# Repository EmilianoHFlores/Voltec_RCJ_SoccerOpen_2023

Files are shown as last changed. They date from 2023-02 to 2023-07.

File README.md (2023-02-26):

# Voltec_RCJ_SoccerOpen_2023
 Source programs. libraries, electronic schematicsm designs and CAD files from the 2023 Voltec Robocup team, participating in TMR 2023 Soccer Open category.

## Arduino Programs
 All arduino libraries and programs are created for running on an ATMEGA-2560 chip. For pin assignments, refer to the pcb schematics and design.

## PCBs
 PCB design files were created on Autodesk Eagle 9.6.2. Library requirements and references are included on folder.

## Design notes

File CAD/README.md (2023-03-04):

## CAD Development
 Full robot design is available at Onshape:  https://cad.onshape.com/documents/feb5a52ba7614c4b1a7fc88d/w/56c9259f389f981d8cc47606/e/bcdc579321adfbcaa5aa0d92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

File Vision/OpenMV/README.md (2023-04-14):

## Development
 All programs in OpenMV vision have been tested on an OPENMV H7 R2 camera and an OPENMV H7 R1. Only standard camera libraries have been used.

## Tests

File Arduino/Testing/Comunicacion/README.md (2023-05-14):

# Comunicación entre arduino y openmv
Este es el sistema de comunicación utilizado entre el controlador y la cámara para transmitir datos de manera organizada
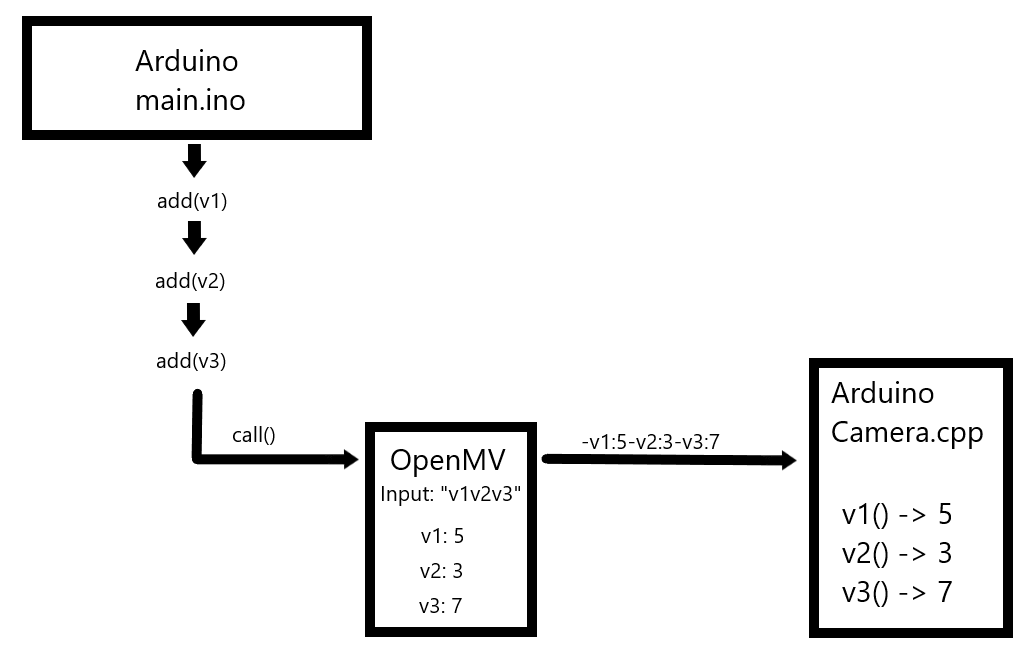
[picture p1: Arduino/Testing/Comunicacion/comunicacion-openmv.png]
Sistema de comunicación entre Arduino y OpenMV

* Ejemplo utilizando Javascript

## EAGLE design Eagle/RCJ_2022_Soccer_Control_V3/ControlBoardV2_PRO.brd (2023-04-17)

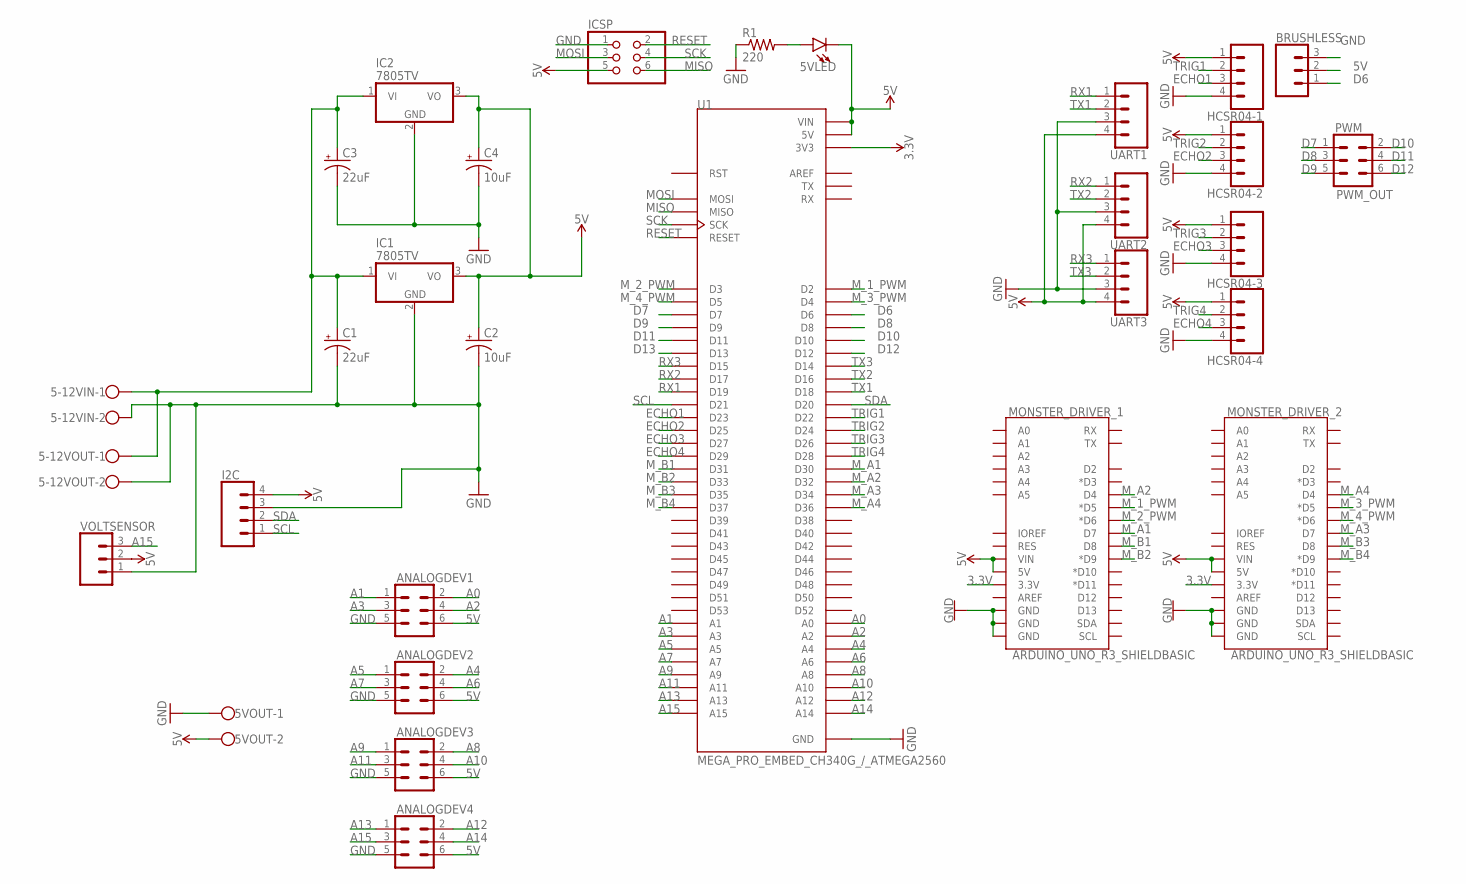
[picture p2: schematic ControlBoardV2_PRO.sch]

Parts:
5-12VIN, 5-12VOUT, 5VOUT: W237-102
5VLED: LED5MM; LED_5MM
ANALOGDEV1, ANALOGDEV2, ANALOGDEV3, ANALOGDEV4: CONN_03X2NO_SILK; 2X3-NS
BRUSHLESS: CONN_03; 1X03
C1, C3: 22uF; E2,5-5
C2, C4: 10uF; E2,5-5
HCSR04-1, HCSR04-2, HCSR04-3, HCSR04-4: CONN_04; 1X04
I2C: CONN_04; 1X04
IC1, IC2: 7805TV; TO220V
ICSP: PINHD-2X3; 2X03
MONSTER_DRIVER_1, MONSTER_DRIVER_2: ARDUINO_UNO_R3_SHIELDBASIC; UNO_R3_SHIELD
PWM: PWM_OUT; 2X3
R1: 220; 0204/7
U1: MEGA_PRO_EMBED_CH340G_/_ATMEGA2560; MODULE_MEGA_PRO_EMBED_CH340G_/_ATMEGA2560
UART1, UART2, UART3: CONN_04; 1X04
VOLTSENSOR: CONN_03; 1X03

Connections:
3.3V: MONSTER_DRIVER_1.3.3V, MONSTER_DRIVER_2.3.3V, U1.3V3_1 (3V3), U1.3V3_2 (3V3)
5V: 5VLED.K (C), 5VOUT.2, ANALOGDEV1.6, ANALOGDEV2.6, ANALOGDEV3.6, ANALOGDEV4.6, BRUSHLESS.2, C2.+, C4.+, HCSR04-1.1, HCSR04-2.1, HCSR04-3.1, HCSR04-4.1, I2C.4, IC1.3 (VO), IC2.3 (VO), ICSP.5, MONSTER_DRIVER_1.5V, MONSTER_DRIVER_1.VIN, MONSTER_DRIVER_2.5V, MONSTER_DRIVER_2.VIN, U1.5V_1 (5V), U1.5V_2 (5V), U1.5V_3 (5V), U1.VIN_1 (VIN), U1.VIN_2 (VIN), UART1.4, UART2.4, UART3.4, VOLTSENSOR.2
A0: ANALOGDEV1.2, U1.A0
A1: ANALOGDEV1.1, U1.A1
A2: ANALOGDEV1.4, U1.A2
A3: ANALOGDEV1.3, U1.A3
A4: ANALOGDEV2.2, U1.A4
A5: ANALOGDEV2.1, U1.A5
A6: ANALOGDEV2.4, U1.A6
A7: ANALOGDEV2.3, U1.A7
A8: ANALOGDEV3.2, U1.A8
A9: ANALOGDEV3.1, U1.A9
A10: ANALOGDEV3.4, U1.A10
A11: ANALOGDEV3.3, U1.A11
A12: ANALOGDEV4.2, U1.A12
A13: ANALOGDEV4.1, U1.A13
A14: ANALOGDEV4.4, U1.A14
A15: ANALOGDEV4.3, U1.A15, VOLTSENSOR.3
D6: BRUSHLESS.1, U1.D6
D7: PWM.1, U1.D7
D8: PWM.3, U1.D8
D9: PWM.5, U1.D9
D10: PWM.2, U1.D10
D11: PWM.4, U1.D11
D12: PWM.6, U1.D12
D13: U1.D13
ECHO1: HCSR04-1.3, U1.D23
ECHO2: HCSR04-2.3, U1.D25
ECHO3: HCSR04-3.3, U1.D27
ECHO4: HCSR04-4.3, U1.D29
GND: 5-12VIN.2, 5-12VOUT.2, 5VOUT.1, ANALOGDEV1.5, ANALOGDEV2.5, ANALOGDEV3.5, ANALOGDEV4.5, BRUSHLESS.3, C1.-, C2.-, C3.-, C4.-, HCSR04-1.4, HCSR04-2.4, HCSR04-3.4, HCSR04-4.4, I2C.3, IC1.2 (GND), IC2.2 (GND), ICSP.1, MONSTER_DRIVER_1.GND@0 (GND), MONSTER_DRIVER_1.GND@1 (GND), MONSTER_DRIVER_1.GND@2 (GND), MONSTER_DRIVER_2.GND@0 (GND), MONSTER_DRIVER_2.GND@1 (GND), MONSTER_DRIVER_2.GND@2 (GND), R1.1, U1.GND_1 (GND), U1.GND_2 (GND), U1.GND_3 (GND), UART1.3, UART2.3, UART3.3, VOLTSENSOR.1
MISO: ICSP.6, U1.MISO
MOSI: ICSP.3, U1.MOSI
M_1_PWM: MONSTER_DRIVER_1.D5 (*D5), U1.D2
M_2_PWM: MONSTER_DRIVER_1.D6 (*D6), U1.D3
M_3_PWM: MONSTER_DRIVER_2.D5 (*D5), U1.D4
M_4_PWM: MONSTER_DRIVER_2.D6 (*D6), U1.D5
M_A1: MONSTER_DRIVER_1.D7, U1.D30
M_A2: MONSTER_DRIVER_1.D4, U1.D32
M_A3: MONSTER_DRIVER_2.D7, U1.D34
M_A4: MONSTER_DRIVER_2.D4, U1.D36
M_B1: MONSTER_DRIVER_1.D8, U1.D31
M_B2: MONSTER_DRIVER_1.D9 (*D9), U1.D33
M_B3: MONSTER_DRIVER_2.D8, U1.D35
M_B4: MONSTER_DRIVER_2.D9 (*D9), U1.D37
unnamed: 5VLED.A, R1.2
unnamed: 5-12VIN.1, 5-12VOUT.1, C1.+, C3.+, IC1.1 (VI), IC2.1 (VI)
RESET: ICSP.2, U1.RESET
RX1: U1.D19, UART1.1
RX2: U1.D17, UART2.1
RX3: U1.D15, UART3.1
SCK: ICSP.4, U1.SCK
SCL: I2C.1, U1.D21
SDA: I2C.2, U1.D20
TRIG1: HCSR04-1.2, U1.D22
TRIG2: HCSR04-2.2, U1.D24
TRIG3: HCSR04-3.2, U1.D26
TRIG4: HCSR04-4.2, U1.D28
TX1: U1.D18, UART1.2
TX2: U1.D16, UART2.2
TX3: U1.D14, UART3.2

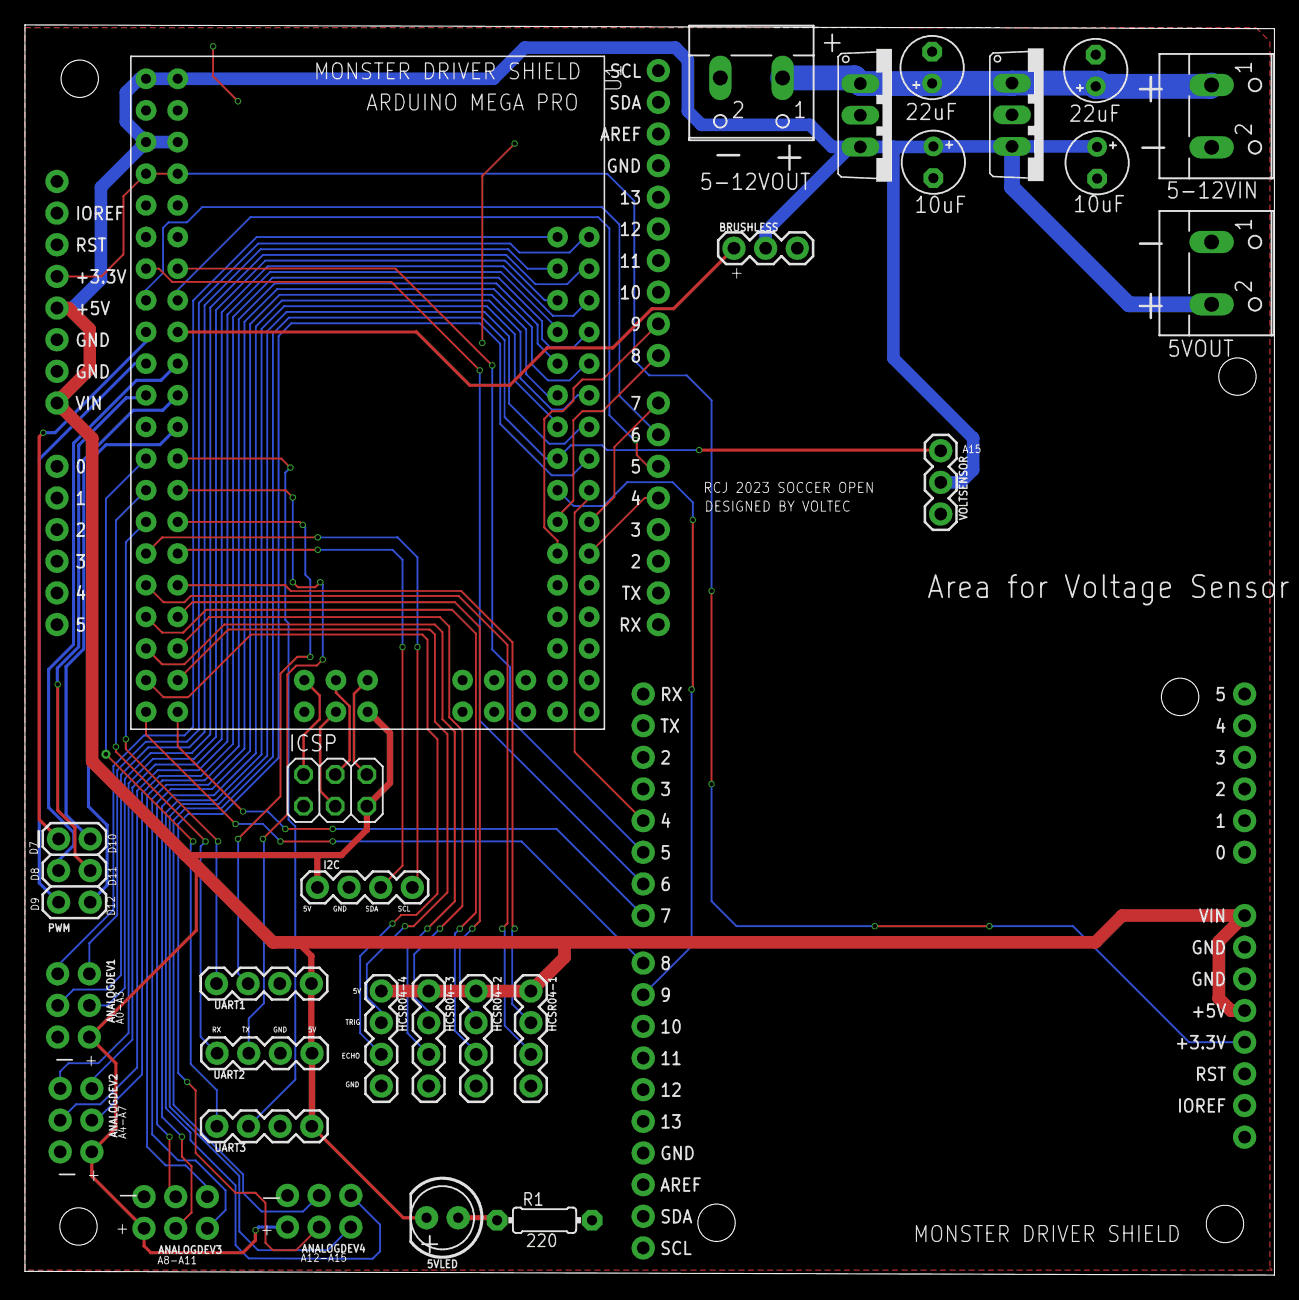
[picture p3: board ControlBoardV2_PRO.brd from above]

Board: 2 copper layers, 100.3 x 100.3 mm, 30 parts (0 on the bottom side), 60 nets.

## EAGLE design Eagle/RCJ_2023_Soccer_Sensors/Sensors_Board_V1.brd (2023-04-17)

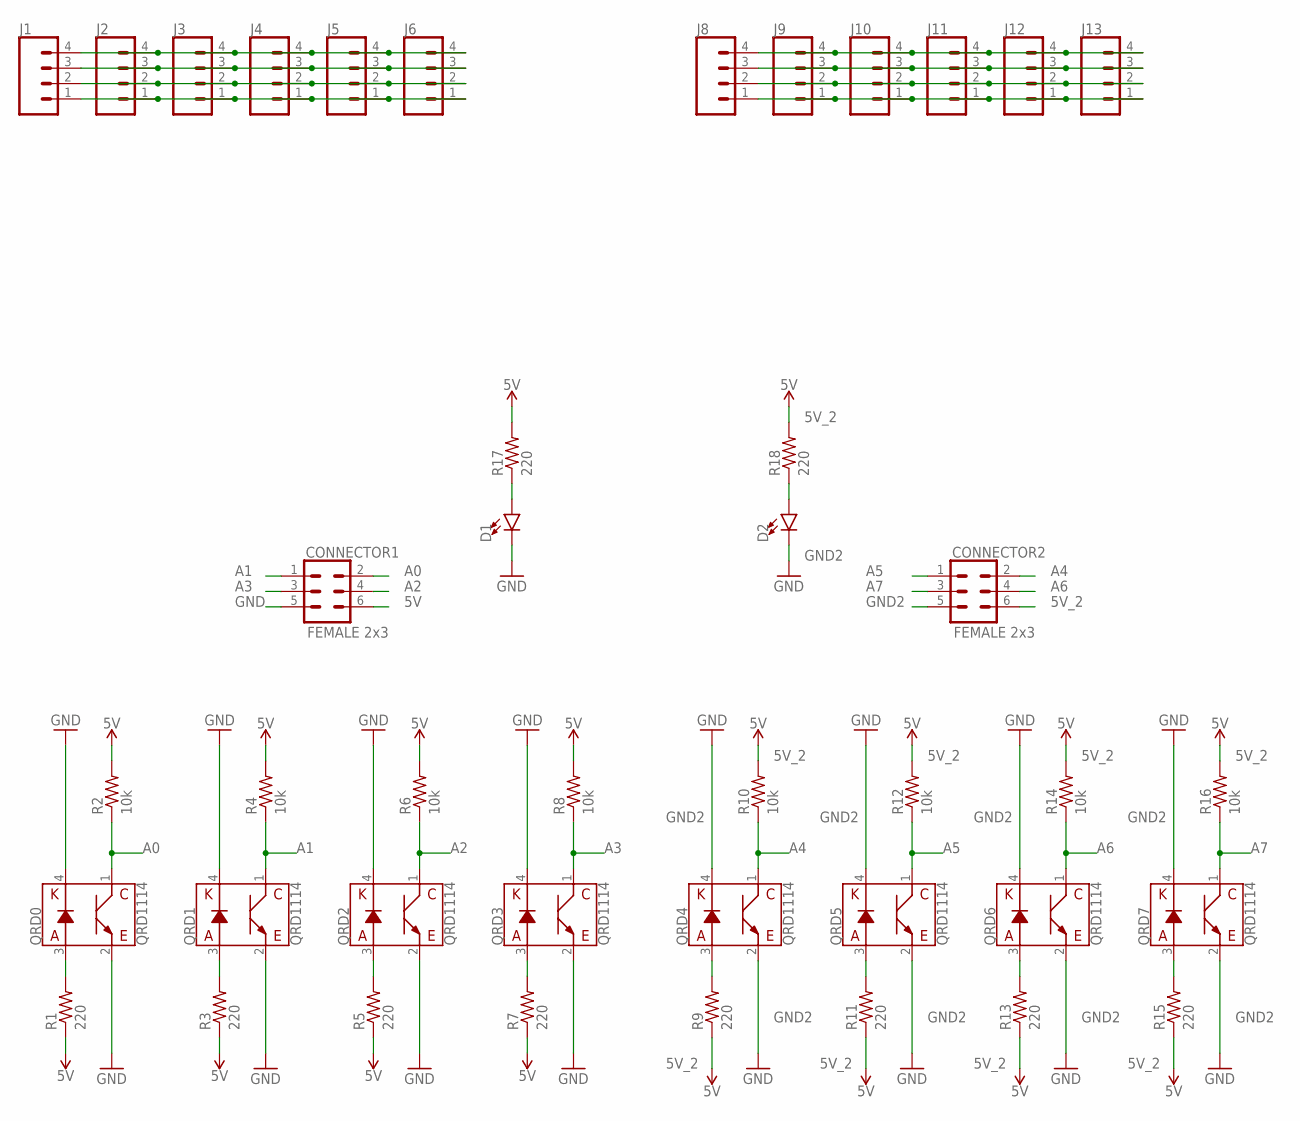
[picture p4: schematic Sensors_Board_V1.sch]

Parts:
CONNECTOR1, CONNECTOR2: FEMALE 2x3; 2X3
D1, D2: LED3MM; LED_3MM
J1, J2, J3, J4, J5, J6, J8, J9, J10, J11, J12, J13: CONN_04; 1X04
QRD0, QRD1, QRD2, QRD3, QRD4, QRD5, QRD6, QRD7: QRD1114
R1, R3, R5, R7, R9, R11, R13, R15, R17, R18: 220; 0204/7
R2, R4, R6, R8, R10, R12, R14, R16: 10k; 0204/7

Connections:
5V: CONNECTOR1.6, R1.1, R2.2, R3.1, R4.2, R5.1, R6.2, R7.1, R8.2, R17.2
5V_2: CONNECTOR2.6, R9.1, R10.2, R11.1, R12.2, R13.1, R14.2, R15.1, R16.2, R18.2
A0: CONNECTOR1.2, QRD0.1 (C), R2.1
A1: CONNECTOR1.1, QRD1.1 (C), R4.1
A2: CONNECTOR1.4, QRD2.1 (C), R6.1
A3: CONNECTOR1.3, QRD3.1 (C), R8.1
A4: CONNECTOR2.2, QRD4.1 (C), R10.1
A5: CONNECTOR2.1, QRD5.1 (C), R12.1
A6: CONNECTOR2.4, QRD6.1 (C), R14.1
A7: CONNECTOR2.3, QRD7.1 (C), R16.1
GND: CONNECTOR1.5, D1.K (C), QRD0.2 (E), QRD0.4 (K), QRD1.2 (E), QRD1.4 (K), QRD2.2 (E), QRD2.4 (K), QRD3.2 (E), QRD3.4 (K)
GND2: CONNECTOR2.5, D2.K (C), QRD4.2 (E), QRD4.4 (K), QRD5.2 (E), QRD5.4 (K), QRD6.2 (E), QRD6.4 (K), QRD7.2 (E), QRD7.4 (K)
unnamed: QRD0.3 (A), R1.2
unnamed: QRD1.3 (A), R3.2
unnamed: QRD2.3 (A), R5.2
unnamed: QRD3.3 (A), R7.2
unnamed: QRD4.3 (A), R9.2
unnamed: QRD5.3 (A), R11.2
unnamed: QRD6.3 (A), R13.2
unnamed: QRD7.3 (A), R15.2
unnamed: D1.A, R17.1
unnamed: D2.A, R18.1
unnamed: J1.4, J2.4, J3.4, J4.4, J5.4, J6.4
unnamed: J1.3, J2.3, J3.3, J4.3, J5.3, J6.3
unnamed: J1.2, J2.2, J3.2, J4.2, J5.2, J6.2
unnamed: J1.1, J2.1, J3.1, J4.1, J5.1, J6.1
unnamed: J8.4, J9.4, J10.4, J11.4, J12.4, J13.4
unnamed: J8.3, J9.3, J10.3, J11.3, J12.3, J13.3
unnamed: J8.2, J9.2, J10.2, J11.2, J12.2, J13.2
unnamed: J8.1, J9.1, J10.1, J11.1, J12.1, J13.1

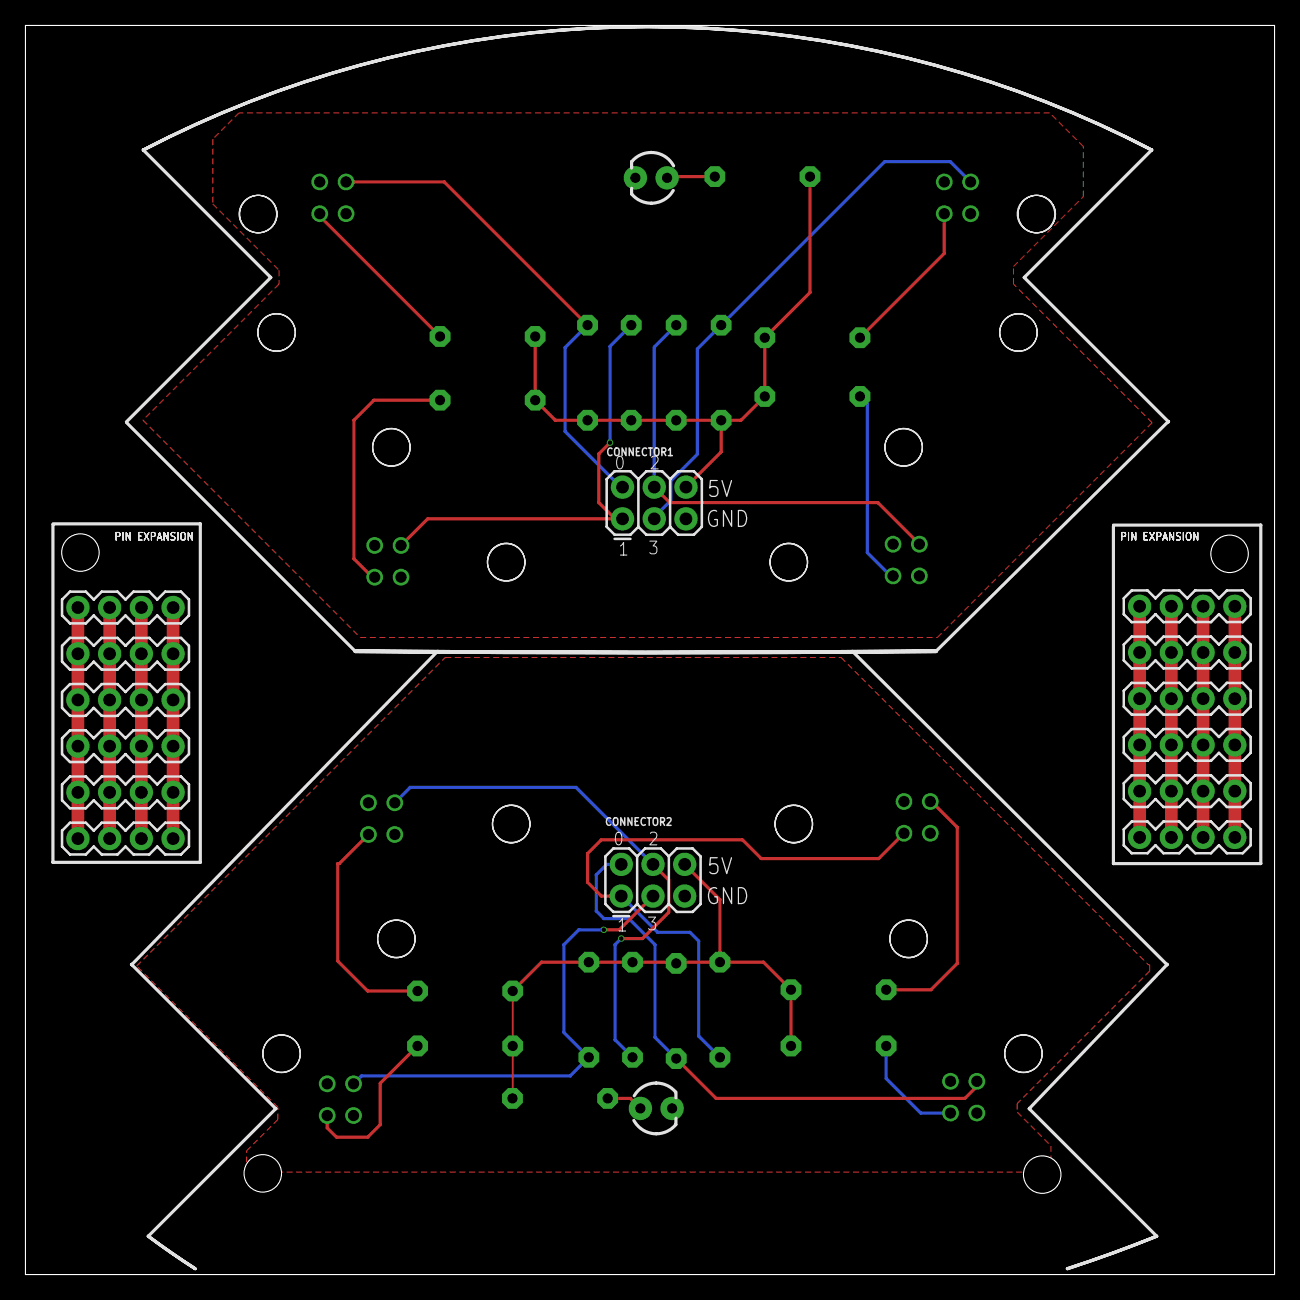
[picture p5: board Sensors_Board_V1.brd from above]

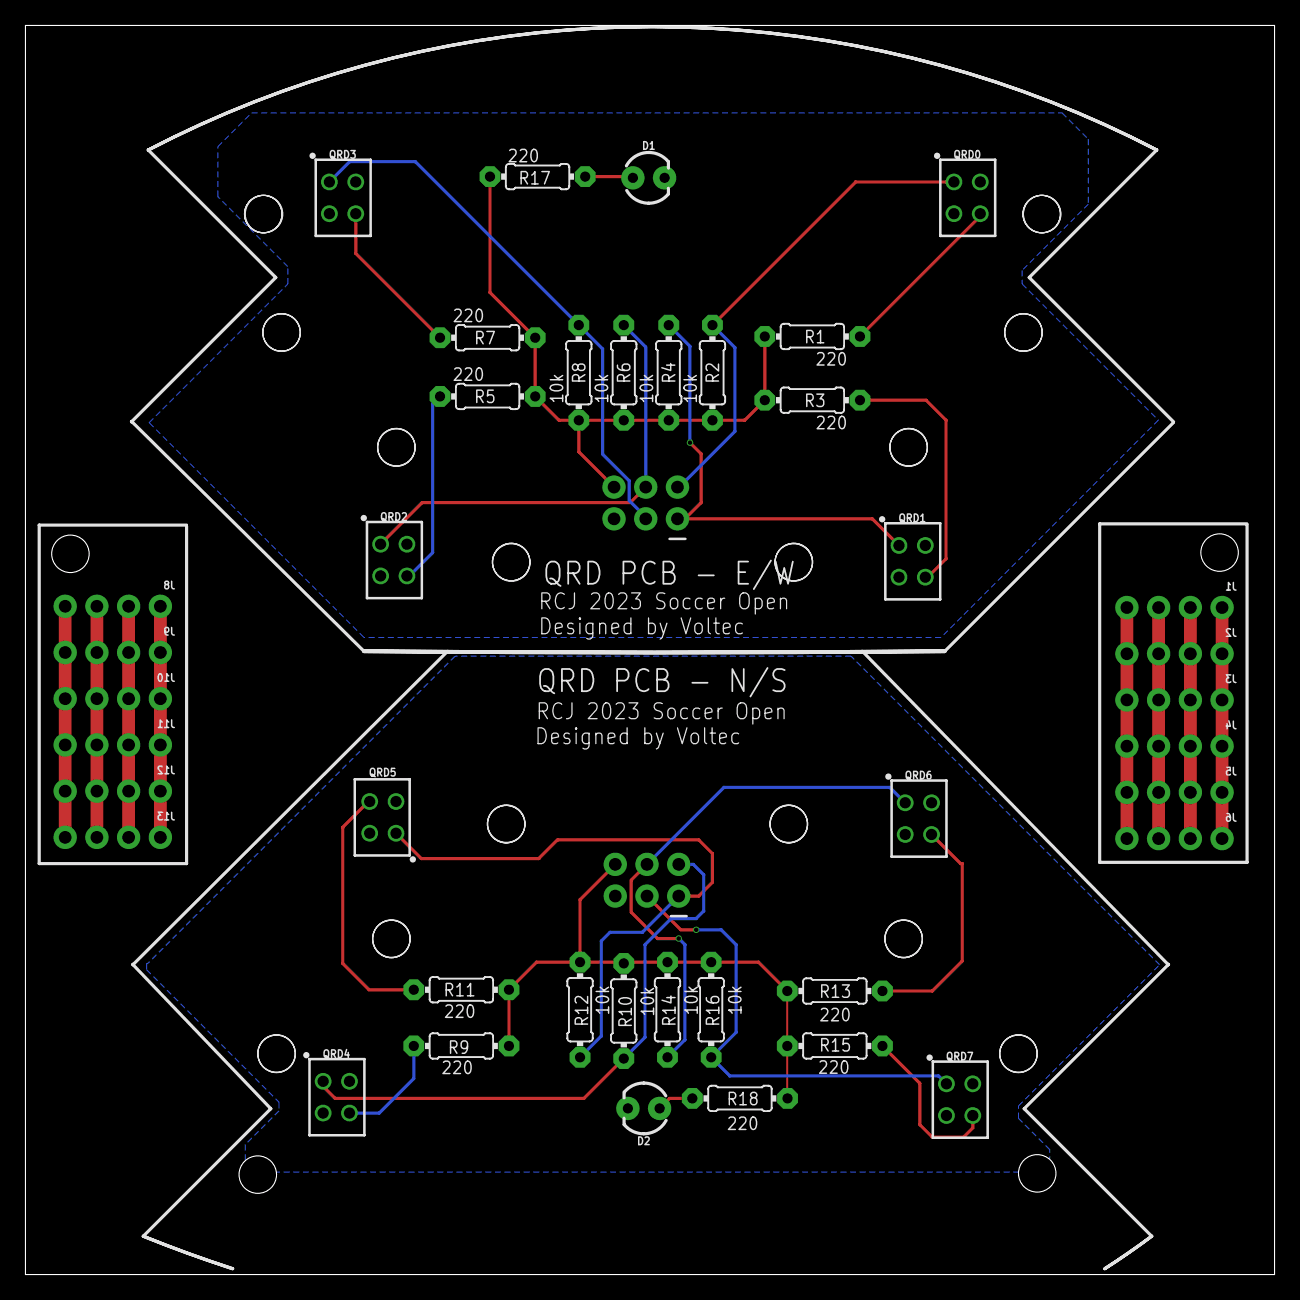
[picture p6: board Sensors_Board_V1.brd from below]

Board: 2 copper layers, 100.0 x 100.0 mm, 42 parts (28 on the bottom side), 30 nets.

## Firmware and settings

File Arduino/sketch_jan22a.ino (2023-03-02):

// Comentarios no hechos

/*
 * -1 = Object not in vision camp
 * 0 = Object at left of the robot vision camp
 * 1 = Object at middle of the robot vision camp
 * 2 = Object at right of the robot vision camp
*/

// Arduino-Native modules
#include <Wire.h>

// Manually installed modules
#include <LiquidCrystal_I2C.h>
#include "AHRSProtocol.h"

// Global constants
#define NWb 2
#define NWa 3
#define SWa 5
#define SWb 4
#define SEa 7
#define SEb 6
#define NEb 8
#define NEa 9
#define buzzer 50
#define buzzerLevel 255
#define defaultDelay 25
#define ITERATION_DELAY_MS 10
#define NAVX_SENSOR_DEVICE_I2C_ADDRESS_7BIT 0x32
#define NUM_BYTES_TO_READ 8
const int QQVGA[2] = { 160, 120 };
const int QVGA[2] = { 320, 240 };
const int VGA[2] = { 640, 480 };
const int HQQVGA[2] = { 120, 80 };
const int HQVGA[2] = { 240, 160 };
const int HVGA[2] = { 480, 320 };
const int *resolution = QVGA;
const int degreeDeviation = 10;
const bool _directionLog = false;
const bool _log = false;
const String ownTeam = "y";
const String enemyTeam = ownTeam == "y" ? "b" : "y";
// Global variables
int maxSpeed = 255;
int rotationSpeed = 100;
int positionSpeed = 25;
int oX, oY, yX, yY, bX, bY;
double oZ, yZ, bZ;
int lastTimeSeen;
int register_address = NAVX_REG_YAW_L;
String oId, yId, bId;
byte data[512];

// Initialize objects

// LiquidCrystal_I2C lcd(0x27, 16, 2);

void setup() {

  Serial.begin(9600);
  println("Serial communication started");

  Serial1.begin(115200);
  Serial1.setTimeout(1);
  println("Serial1 communication started");

  Wire.begin();
  for (int i = 0; i < sizeof(data); i++) {
    data[i] = 0;
  }

  // lcd.begin(16, 2);
  // lcd.backlight();
  // println("LCD screen added");

  pinMode(NEa, OUTPUT);
  pinMode(NEb, OUTPUT);
  pinMode(SWa, OUTPUT);
  pinMode(SWb, OUTPUT);
  pinMode(SEa, OUTPUT);
  pinMode(SEb, OUTPUT);
  pinMode(NWa, OUTPUT);
  pinMode(NWb, OUTPUT);
  println("Motors added");
  stop(5000, true);

  pinMode(buzzer, OUTPUT);
  digitalWrite(buzzer, LOW);
  println("Buzzer Added");
}

// Local loop function variables
bool endWhileLoop1 = false;
bool endWhileLoop2 = false;
bool endWhileLoop3 = false;
float ballDegrees = 420;

void loop() {
  endWhileLoop1 = false;
  endWhileLoop2 = false;
  endWhileLoop3 = false;
  callOrange();
  if (checkBallDirection() < 0) {
    TurnRight(maxSpeed);
  } else {
    if (ballDegrees == 420) {
      do {
        callOrange();
        int preciseLocation = checkPreciseBallDirection(7);
        switch (preciseLocation) {
          case -1:
            endWhileLoop1 = true;
            break;
          case 0:
          case 1:
            TurnLeft(rotationSpeed);
            break;
          case 2:
          case 3:
          case 4:
            ballDegrees = to360angle(checkDegrees());
            break;
          case 5:
          case 6:
            TurnRight(rotationSpeed);
            break;
        }
      } while (!endWhileLoop1);
    } else {
      rotateToAngle(to360angle(checkDegrees()), 0);
      int diferencia = (ballDegrees <= 180 ? 60 : -60);
      int total = int(ballDegrees) + diferencia;
      oX = -1;
      oY = -1;
      oZ = -1;      
      do {
        moveToAngle(total, maxSpeed);
        callOrange();
        if (oX > 1) {
          endWhileLoop2 = true;
        }
      } while (!endWhileLoop2);
      do {
        Serial.println(ballDegrees);
        callOrange();
        int preciseLocation = checkPreciseBallDirection(7);
        switch (preciseLocation) {
          case -1: 
            endWhileLoop3 = true;
            break;
          case 0:
          case 1:
            TurnLeft(positionSpeed);
            break;
          case 2:
          case 3:,
          case 4:
            North(maxSpeed, 1000);
            break;
          case 5:
          case 6:
            TurnRight(positionSpeed);
            break;
        }
      } while (!endWhileLoop3);

      ballDegrees = 420;
    }
  }
}

void rotateToAngle(float actualAngle, float destineAngle) {
  while (actualAngle <= destineAngle - degreeDeviation) {
    TurnRight(rotationSpeed);
    actualAngle = checkDegrees();
  }
  while (actualAngle >= destineAngle + degreeDeviation) {
    TurnLeft(rotationSpeed);
    actualAngle = checkDegrees();
  }
  stop();
}

float to360angle(float actualAngle) {
  return actualAngle > 0 ? actualAngle : 360 + actualAngle;
}

/*
 * @returns {float} Robot will return the angle the robot is looking to, from -179.99 to +179.99
 * @example
 * float degree = checkDegrees();
 * rotateToAngle(degree + 90)
 * // Robot will move 90 degrees right from its original position
*/
float checkDegrees() {
  int i;
  Wire.beginTransmission(NAVX_SENSOR_DEVICE_I2C_ADDRESS_7BIT);  // Begin transmitting to navX-Sensor
  Wire.write(register_address);                                 // Sends starting register address
  Wire.write(NUM_BYTES_TO_READ);                                // Send number of bytes to read
  Wire.endTransmission();                                       // Stop transmitting

  /* Receive the echoed value back */
  Wire.beginTransmission(NAVX_SENSOR_DEVICE_I2C_ADDRESS_7BIT);               // Begin transmitting to navX-Sensor
  Wire.requestFrom(NAVX_SENSOR_DEVICE_I2C_ADDRESS_7BIT, NUM_BYTES_TO_READ);  // Send number of bytes to read
  delay(1);
  while (Wire.available()) {  // Read data (slave may send less than requested)
    data[i++] = Wire.read();
  }
  Wire.endTransmission();  // Stop transmitting
  return IMURegisters::decodeProtocolSignedHundredthsFloat((char *)&data[0]);
}

/*
 * @param {String} type The prefix of the variable, oX, yX, bX, etc.
 * @returns {void} Prints to the serial monitor all variables
 * @example
 * callOrange();
 * logCoordinatesVariables("o");
 * // This function will call the camera for new data and print the values to the Serial Monitor.
*/
void logCoordinatesVariables(String type) {
  println("Starting Log Coordinates Variables function...");
  if (type == "o") {
    Serial.print("oX: ");
    Serial.print(oX);
    Serial.print(", oY: ");
    Serial.print(oY);
    Serial.print(", oZ: ");
    Serial.print(oZ);
    Serial.print(", oId: ");
    Serial.println(oId);
  } else if (type == "b") {
    Serial.print("bX: ");
    Serial.print(bX);
    Serial.print(", bY: ");
    Serial.print(bY);
    Serial.print(", bZ: ");
    Serial.print(bZ);
    Serial.print(", bId: ");
    Serial.println(bId);
  } else if (type == "y") {
    Serial.print("yX: ");
    Serial.print(yX);
    Serial.print(", yY: ");
    Serial.print(yY);
    Serial.print(", yZ: ");
    Serial.print(yZ);
    Serial.print(", yId: ");
    Serial.println(yId);
  }
  println("Log Coordinates Variables function excecuted successfully...");
}
/*
 * @returns {void} Calls the camera for Orange and then excecutes the substring function
 * @example
 * callOrange();
 * // oX, oY, oZ and oId variables will be updated
*/
void callOrange() {
  println("Starting Call Orange function...");
  Serial1.write("o");
  for (int i = 0; i < 10; i++) {
    println("Esperando...");
    if (Serial1.available()) break;
    delay(1);
  }

  if (Serial1.available()) {
    substringData(Serial1.readString());
  }
  println("Call Orange function excecuted successfully");
}

/*
 * @returns {void} Calls the camera for Yellow and then excecutes the substring function
 * @example
 * callYellowGoal();
 * // yX, yY, yZ and yId variables will be updated
*/
void callYellowGoal() {
  println("Starting Call Yellow Goal function...");
  Serial1.write("y");

  for (int i = 0; i < 10; i++) {
    println("Esperando...");
    if (Serial1.available()) break;
    delay(1);
  }

  if (Serial1.available()) {
    substringData(Serial1.readString());
  }
  println("Call Yellow Goal function excecuted successfully");
}

/*
 * @returns {void} Calls the camera for Orange and then excecutes the substring function
 * @example
 * callBlueGoal();
 * // bX, bY, bZ and bId variables will be updated
*/
void callBlueGoal() {
  println("Starting Call Blue Goal function...");
  Serial1.write("b");
  for (int i = 0; i < 10; i++) {
    println("Esperando...");
    if (Serial1.available()) break;
    delay(1);
  }

  if (Serial1.available()) {
    substringData(Serial1.readString());
  }
  println("Call Blue Goal function excecuted successfully");
}

/*
 * @param {String} type The ID of the goal to follow, ("y" for yellow, "b" for blue)
 * @returns {void} Function will change xX, xY, xZ, and xId variables and move the robot to type goal 
 * @example
 * followGoal("y");
 * // Robot will find the path up to the Y goal
*/
void followGoal(String type) {
  println("Starting Follow Goal function...");
  int typeInt = 0;
  if (type == "b") typeInt = 1;
  switch (typeInt) {
    case 0:
      if (yX >= 0) {
        if (yX <= (resolution[0] / 3)) NorthWest(maxSpeed);
        else if (yX > (resolution[0] / 3) && yX < ((resolution[0] / 3) * 2)) North(maxSpeed);
        else if (yX >= ((resolution[0] / 3) * 2)) NorthEast(maxSpeed);
      } else TurnRight(rotationSpeed);
      break;
    case 1:
      if (bX >= 0) {
        if (bX <= (resolution[0] / 3)) NorthWest(maxSpeed);
        else if (bX > (resolution[0] / 3) && bX < ((resolution[0] / 3) * 2)) North(maxSpeed);
        else if (bX >= ((resolution[0] / 3) * 2)) NorthEast(maxSpeed);
      } else TurnRight(rotationSpeed);
      break;
    default:
      println("Unrecognized goal type");
      break;
  }
  println("Follow Goal function excecuted successfully");
}

/*
 * @returns {void} Function will change oX, oY, oZ, and oId variables and move the robot to the ball
 * @example
 * followBall();
 * // Robot will find the path up to the ball
*/
void followBall() {
  println("Starting Follow Ball function...");
  if (oX >= 0) {
    if (oX <= (resolution[0] / 3)) {
      NorthWest(maxSpeed);
      lastTimeSeen = 0;
    } else if (oX > (resolution[0] / 3) && oX < ((resolution[0] / 3) * 2)) {
      North(maxSpeed);
      lastTimeSeen = 1;
    } else if (oX >= ((resolution[0] / 3) * 2)) {
      NorthEast(maxSpeed);
      lastTimeSeen = 2;
    }
  } else {
    if (lastTimeSeen == 0) TurnLeft(rotationSpeed);
    else if (lastTimeSeen == 2) TurnRight(rotationSpeed);
    else TurnRight(rotationSpeed);
  }
  println("Follow Ball function excecuted successfully");
}

/*
 * Function will work based on oX, oY, oZ and oId values
 * A call to the camera must be perfomemd before executing this function
 * @returns {Int}
 * -1 When the ball is not in vision range of the robot
 * 0 When the ball is at the left of the robot
 * 1 When the ball is in the middle of the robot
 * 2 When the ball is in the right of the robot
 * @example
 * int location = checkBallDirection();
 * // Robot will save in 'location' variable where the ball is
*/
int checkBallDirection() {
  println("Starting Check Ball Direction function...");
  if (oX >= 0) {
    println("Check Ball Direction function excecuted successfully");
    if (oX <= (resolution[0] / 3)) return 0;
    if (oX > (resolution[0] / 3) && oX < (resolution[0] / 3) * 2) return 1;
    if (oX >= ((resolution[0] / 3) * 2)) return 2;
  }
  println("Check Ball Direction function excecuted successfully");
  return -1;
}

/*
 * Function will work based on oX, oY, oZ and oId values
 * A call to the camera must be performed before executing this function
 * @param {Int} splits The amount of equally-sized sections to the ball be found in
 * @returns {Int} The function will return where is the ball located in one section of the amount specified
*/
int checkPreciseBallDirection(int splits) {
  println("Starting Check Ball Direction function...");
  if (oX >= 0) {
    println("Check Ball Direction function excecuted successfully");
    if (oX <= (resolution[0] / splits)) return 0;
    for (int i = 1; i < splits; i++) {
      if (oX > ((resolution[0] / splits) * i) && oX < ((resolution[0] / splits) * (i + 1))) return i - 1;
    }
    return splits - 1;
  }
  println("Check Ball Direction function excecuted successfully");
  return -1;
}


/*
 * Function will work based on xX, xY, xZ and xId values
 * A call to the camera must be perfomemd before executing this function
 * @param {String} type The goal type to detect, "y" or "b"
 * @returns
 * -1 When the goal is not in vision range of the robot
 * 0 When the goal is at the left of the robot
 * 1 When the goal is in the middle of the robot
 * 2 When the goal is in the right of the robot
 * @example
 * int location = checkGoalDirection();
 * // Robot will save in 'location' variable where the ball is
*/
int checkGoalDirection(String type) {
  println("Starting Check Goal Direction function...");
  int typeInt = 0;
  if (type == "b") typeInt = 1;
  switch (typeInt) {
    case 0:
      println("Check Goal Direction function excecuted successfully");
      if (yX >= 0) {
        if (yX <= (resolution[0] / 3)) return 0;
        else if (yX > (resolution[0] / 3) && yX < ((resolution[0] / 3) * 2)) return 1;
        else if (yX >= ((resolution[0] / 3) * 2)) return 2;
      }
      return -1;
      break;
    case 1:
      println("Check Goal Direction function excecuted successfully");
      if (bX >= 0) {
        if (bX <= (resolution[0] / 3)) return 0;
        else if (bX > (resolution[0] / 3) && bX < (resolution[0] / 3) * 2) return 1;
        else if (bX >= ((resolution[0] / 3) * 2)) return 2;
      }
      return -1;
      break;
    default:
      println("Unspecified goal type");
      break;
  }
}

/*
 * @param {String} data Data is raw information received from the camera.
 * @returns {void} Robot will change xX, xY, xZ and xId variables depending on the given data
 * @example
 * substringData("x:10,y:20,z:5,id:o")
*/
void substringData(String data) {
  println("Starting Substring Data function...");
  print("Data: ");
  println(data);
  int initIndex = data.indexOf(",");
  int middleIndex = data.indexOf(",", initIndex + 1);
  int lastIndex = data.lastIndexOf(",");
  int x = data.substring(2, initIndex).toInt();
  int y = data.substring(initIndex + 3, middleIndex).toInt();
  double z = data.substring(middleIndex + 3, lastIndex).toDouble();
  String id = data.substring(lastIndex + 4, data.length());
  if (id == "o") {
    oX = x;
    oY = y;
    oZ = z;
    oId = id;
  } else if (id == "y") {
    yX = x;
    yY = y;
    yZ = z;
    yId = id;
  } else if (id == "b") {
    bX = x;
    bY = y;
    bZ = z;
    bId = id;
  } else {
    print(id);
    print(" - ");
    println("Range Error: ID not recognized");
  }
  println("Substring Data function excecuted successfully");
}

/*
 * @param {Int} d is the amount of milliseconds of delay, from 0 to Infinity
 * @returns {void} Robot will alternate between turning on and off the buzzer but everytime faster
 * @example
 * println("Starting in 5 seconds...");
 * buzzerDelay(5000);
 * println("Started.")
*/
void buzzerDelay(int d) {
  println("Starting Buzzer Delay function...");
  const float max = (d / 3);
  const float mid = (d / 3);
  const float min = (d / 3);
  for (int i = 0; i <= (max / 200); i++) {
    analogWrite(buzzer, buzzerLevel);
    delay(100);
    analogWrite(buzzer, LOW);
    delay(100);
  }
  for (int i = 0; i < (mid / 100); i++) {
    analogWrite(buzzer, buzzerLevel);
    delay(50);
    analogWrite(buzzer, LOW);
    delay(50);
  }
  for (int i = 0; i < (mid / 50); i++) {
    analogWrite(buzzer, buzzerLevel);
    delay(25);
    analogWrite(buzzer, LOW);
    delay(25);
  }
  println("Buzzer Delay function completed successfully");
}

/*
 * @param {int, required} angle
 * angle is the angle the robot will move, from 0 to 359
 * @param {int, required} speed
 * the maximum speed the robot will move, from 0 to 255
 * @param {int} d
 * The amount of time the robot will keep moving, from 0 to Infinity
 * @returns;
 * The robot will move to the specified angle at the specified speed
 * @example;
 * moveToAngle(90, 100);
 * // Robot will move to angle 90 at a maximum speed of 100
*/
void moveToAngle(int angle, int speed) {
  println("Starting Move to Angle function");
  int NW_speed = speed * cos((PI / 180) * (angle + 315));
  int SW_speed = speed * cos((PI / 180) * (angle + 225));
  int SE_speed = speed * cos((PI / 180) * (angle + 135));
  int NE_speed = speed * cos((PI / 180) * (angle + 45));
  int _largestNumber = largestNumber(abs(NW_speed), abs(SW_speed), abs(SE_speed), abs(NE_speed));
  float ratio = float(speed) / float(_largestNumber);
  NW_speed *= ratio;
  SW_speed *= -ratio;
  SE_speed *= -ratio;
  NE_speed *= ratio;
  _NW(NW_speed);
  _SW(SW_speed);
  _SE(SE_speed);
  _NE(NE_speed);
  println("Move to Angle function completed successfully");
}
void moveToAngle(int angle, int speed, int d) {
  println("Starting Move to Angle function");
  int NW_speed = speed * cos((PI / 180) * (angle + 315));
  int SW_speed = -speed * cos((PI / 180) * (angle + 225));
  int SE_speed = -speed * cos((PI / 180) * (angle + 135));
  int NE_speed = speed * cos((PI / 180) * (angle + 45));
  int _largestNumber = largestNumber(abs(NW_speed), abs(SW_speed), abs(SE_speed), abs(NE_speed));
  float ratio = float(speed) / float(_largestNumber);
  NW_speed *= ratio;
  SW_speed *= ratio;
  SE_speed *= ratio;
  NE_speed *= ratio;
  _NW(NW_speed);
  _SW(SW_speed);
  _SE(SE_speed);
  _NE(NE_speed);
  delay(d);
  println("Move to Angle function completed successfully");
}

/*
 * @param {int, required} number1
 * Integer number from -Infinity to Infinity
 * @param {int, required} number2
 * Integer number from -Infinity to Infinity
 * @param {int, required} number3 
 * Integer number from -Infinity to Infinity
 * @param {int, required} number4
 * Integer number from -Infinity to Infinity
 * @returns int
 * Robot will return the largest number from four of the specified numbers
 * @example
 * int largest = largestNumber(10, 15, 20, 25);
 * Serial.println(largest)
 * // Output: 25
*/
int largestNumber(int number1, int number2, int number3, int number4) {
  println("Starting LargestNumber function...");
  int numbers[] = { number1, number2, number3, number4 };
  int largest = numbers[0];
  for (int i = 1; i < 4; i++)
    if (numbers[i] > largest) largest = numbers[i];
  println("LargestNumber function completed successfully");
  return largest;
}

/*
 * @warning
 * _log must be true for the function to work
 * @param {String, int, required} action 
 * The action that will be printed to Serial Monitior
 * @param {bool} movement
 * If the action is part of motor-movement
 * @returns;
 * Action will be printed to Serial Monitor without a line jump
 * @example
 * print("Hello, World!", false);
 * // Output: Hello, World!
 * _directionLog = false
 * print("Going North-West", true)
 * // Output: 
 * _directionLog = true
 * print("Going North-West", true)
 * // Output: Going North-West
*/
void print(String action) {
  if (_log == true) {
    Serial.print(action);
  }
}
void print(String action, bool movement) {
  if (movement && _directionLog) {
    Serial.print(action);
  } else if (_log && !_directionLog) {
    Serial.print(action);
  } else if (!movement && !_directionLog) {
    Serial.print(action);
  }
}
void print(int action) {
  if (_log == true) {
    Serial.print(action);
  }
}
void print(int action, bool movement) {
  if (movement && _directionLog) {
    Serial.print(action);
  } else if (_log && !_directionLog) {
    Serial.print(action);
  } else if (!movement && !_directionLog) {
    Serial.print(action);
  }
}

/*
 * @warning
 * _log must be true for the function to work
 * @param {String, int, required} action
 * The action that will be printed to Serial Monitior
 * @param {bool} movement
 * If the action is part of motor-movement
 * @returns;
 * Action will be printed to Serial Monitor with a line jump
 * @example
 * print("Hello, World!", false);
 * // Output: Hello, World!
 * _directionLog = false
 * print("Going North-West", true)
 * // Output: 
 * _directionLog = true
 * print("Going North-West", true)
 * // Output: Going North-West
*/
void println(int action) {
  if (_log == true) {
    Serial.println(action);
    // lcd.clear();
    // lcd.print(action);
  }
}
void println(int action, bool movement) {
  if (movement && _directionLog) {
    Serial.println(action);
  } else if (_log && !_directionLog) {
    Serial.println(action);
  } else if (!movement && !_directionLog) {
    Serial.println(action);
  }
}
void println(String action) {
  if (_log == true) {
    Serial.println(action);
    // lcd.clear();
    // lcd.print(action);
  }
}
void println(String action, bool movement) {
  if (movement && _directionLog) {
    Serial.println(action);
  } else if (_log && !_directionLog) {
    Serial.println(action);
  } else if (!movement && !_directionLog) {
    Serial.println(action);
  }
}

/*
 * @param {int} d
 * the amount of time in milliseconds from 0 to Infinity the robot will remain stopped
 * @param {int} b
 * The amount of time in milliseconds from 0 to Infinity the robot will remain stopped but with buzzer activated
 * @returns;
 * Robot will fully stop motor-movement
 * @example
 * stop(1000, true);
 * // Robot will stop for 1 second with the buzzer active before continue with the code
*/
void stop() {
  println("Robot stopped");
  _NW(0, 0);
  _NE(0, 0);
  _SW(0, 0);
  _SE(0, 0);
}
void stop(int d) {
  println("Robot stopped", true);
  _NW(0, 0);
  _NE(0, 0);
  _SW(0, 0);
  _SE(0, 0);
  delay(d);
}
void stop(int d, bool b) {
  println("Robot stopped", true);
  _NW(0, 0);
  _NE(0, 0);
  _SW(0, 0);
  _SE(0, 0);
  if (b == true) buzzerDelay(d);
  else delay(d);
}

/*
 * @param {int, required} speed
 * The maximum speed the robot will move, from 0 to 255
 * @param {int} d
 * The amount of delay in milliseconds the robot will be moving, from 0 to Infinity
 * @returns;
 * The robot will turn on its own axis to the right
 * @example
 * TurnRight(255, 100);
 * // The robot will be moving to the Right at a speed of 255 during 100 milliseconds
*/
void TurnRight(int speed) {
  _NW(0, speed);
  _NE(1, speed);
  _SW(0, speed);
  _SE(1, speed);
  println("Robot turning right", true);
}
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

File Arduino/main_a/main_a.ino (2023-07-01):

#include "Strategy.h"
#include "Qrd.h"

#define VOLUME 10
#define TOGGLE_SWITCH 40
#define START_SWITCH 41
#define COMPASS_TYPE "navx"
#define HELPER_COMPASS "adafruit"
#define START_TIME 5000
#define PREFERRED_ACTION 2
#define TEAM "yellow"
#define REQUIRE_BUTTON true

unsigned long previousMillis = millis();
unsigned long currentMillis = millis();
unsigned long qrdMillis = millis();
unsigned long loopId;

Strategy strategy;
Qrd qrd;

void setup () {
  Serial.begin(115200);
  Serial.setTimeout(50);
  pinMode(START_SWITCH, INPUT);
  pinMode(TOGGLE_SWITCH, INPUT);

  strategy.begin(TEAM);
  strategy.dribbler.begin(6, 7);
  strategy.buzzer.begin(10);
  
  strategy.buzzer.beep(VOLUME);
  delay(250);
  strategy.buzzer.stop();

  strategy.camera.begin();
  strategy.pixy.begin();

  strategy.xbee.begin();
  strategy.motor.begin(2, 33, 32, 5, 38, 39, 3, 34, 35, 4, 36, 37);
  strategy.compass.begin(COMPASS_TYPE);
  strategy.motor.attachCompass(&strategy.compass);
  strategy.motor.helper.begin(HELPER_COMPASS);
  strategy.ultrasonic.begin(25, 24, 23, 22, 27, 26);
  qrd.begin(99, A12, A14, A13,  99, 99, 99, 99,  A7, A4, A6, A5,  A3, A0, A2, A1);

  unsigned long start_millis = millis();
  strategy.buzzer.startTimer();
  for (;;) {
    if (millis() - start_millis >= START_TIME) break;
    strategy.buzzer.beeps(2, VOLUME);
  }
  strategy.buzzer.stop();
  strategy.buzzer.startTimer();
  for (;;) {
    if (digitalRead(START_SWITCH) || !REQUIRE_BUTTON) break;
    strategy.buzzer.beeps(3, VOLUME);
    Serial.println("Waiting for human...");
  }
  strategy.buzzer.stop();
}

bool dribbling = false;
bool firstDribbling = true;
unsigned long start;

unsigned long long previousQrd = 0;
void loopa () {
  strategy.motor.North(200);
  if (millis() - previousQrd >= 25) {
    Serial.println();
    bool north = qrd.North(true);
    if (north) {
      strategy.motor.Stop();
      strategy.motor.South(200);
      delay(400);
      strategy.motor.Stop();
      for (int i = 0; i < 25; i++) qrd.North(false);
    }
    previousQrd = millis();
  }
}

// void loop () {
//   Serial.print("  Navx: "); Serial.print(strategy.compass.checkAngle());
//   Serial.print("  Helper: "); Serial.print(strategy.motor.helper.checkAngle());
//   Serial.print("  Navx initial: "); Serial.print(strategy.compass.initialReading);
//   Serial.print("  Helper initial: "); Serial.println(strategy.motor.helper.initialReading);
//   strategy.motor.rotateToAngle(strategy.compass.checkAngle(), 0, true);
// }

void loop () {
  if (!digitalRead(TOGGLE_SWITCH)) strategy.motor.active(false);
  else strategy.motor.active(true);

  strategy.camera.add("ox");
  strategy.camera.add("oy");
  strategy.camera.add("yi");
  strategy.camera.add("yx");
  strategy.camera.add("yw");
  strategy.camera.call();
  strategy.pixy.getBlocks();

  if (strategy.camera.ox() == -1 && !dribbling) {
    strategy.dribbler.stop();
    if (strategy.pixy.ox() != -1) {
      float angle = strategy.compass.checkAngle();

      strategy.motor.rotateToAngle(
        angle,
        180,
        true
      );
      dribbling = true;
      start = millis();
      return;
    }

    strategy.endAction();
    strategy.passiveDeffense();
    return;
  }

  if (dribbling) {
    if (strategy.camera.ox() == -1) {
      if (millis() - start <= 100) return;
      strategy.buzzer.beep(255);
      delay(500);
      strategy.buzzer.stop();
      strategy.motor.rotateToAngle(strategy.compass.checkAngle(), 0, true);
      dribbling = false;
      return;
    }
    if (strategy.camera.oy() > 10) {
      strategy.goto_ball(100);
    } else if (strategy.camera.oy() >= 3) {
      strategy.goto_ball(60);
      strategy.dribbler.run(50);
    } else if (strategy.camera.oy() == 0) {
      if (firstDribbling) {
        start = millis();
        firstDribbling = false;
      }
      if (millis() - start <= 1000) {
        strategy.goto_ball(50);
        return;
      }
      strategy.dribbler.run(100);
      if (strategy.compass.checkAngle() < 0) strategy.motor.TurnLeft(90);
      else strategy.motor.TurnRight(90);
    }

    if (strategy.compass.range(strategy.compass.checkAngle(), 0, 10)) {
      strategy.dribbler.stop();
      strategy.motor.Stop();
      dribbling = false;
      return;
    }
  } else {
    strategy.dribbler.stop();
    strategy.deffend();
  }
}

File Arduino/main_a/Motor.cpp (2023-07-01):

#include <Arduino.h>
#include "Motor.h"
#include "Pid.h"

#define COMPASS_DEVIATION 15
#define REFRESH_RATE 5 * 1000

Motor::Motor() {
  compassP.kp = 1.8;
  compassP.ki = .1;
  compassP.kd = 1.3;
  compassP.minOutput = 30;
  compassP.maxOutput = 255;
  compassP.delay = 20;
  compassP.errorThreshold = 5;
  compassP.maxErrorSum = 180;

  stability.kp = 1.5;
  stability.ki = .1;
  stability.kd = 1;
  stability.minOutput = 0;
  stability.maxOutput = 30;
  stability.delay = 20;
  stability.errorThreshold = 3;
  stability.maxErrorSum = 180;
}

void Motor::attachCompass (Compass * c) {
  compass = c;
};

void Motor::begin (byte nwpwm, byte nwa, byte nwb, byte nepwm, byte nea, byte neb, byte swpwm, byte swa, byte swb, byte sepwm, byte sea, byte seb) {
  _NE = {nea, neb, nepwm, 0, nea, neb};
  _NW = {nwa, nwb, nwpwm, 0, nwa, nwb};
  _SE = {sea, seb, sepwm, 0, sea, seb};
  _SW = {swa, swb, swpwm, 0, swa, swb};

  pinMode(_SE.pwm, OUTPUT);
  pinMode(_SW.pwm, OUTPUT);
  pinMode(_NE.pwm, OUTPUT);
  pinMode(_NW.pwm, OUTPUT);

  pinMode(_SE.b, OUTPUT);
  pinMode(_SW.b, OUTPUT);
  pinMode(_NE.b, OUTPUT);
  pinMode(_NW.b, OUTPUT);

  pinMode(_SE.a, OUTPUT);
  pinMode(_SW.a, OUTPUT);
  pinMode(_NE.a, OUTPUT);
  pinMode(_NW.a, OUTPUT);
}

void Motor::active(bool state) {
  if (state) {
    if (_NE.a != 50) return;
    _NE.a = _NE.originalA;
    _NE.b = _NE.originalB;
    _NW.a = _NW.originalA;
    _NW.b = _NW.originalB;
    _SE.a = _SE.originalA;
    _SE.b = _SE.originalB;
    _SW.a = _SW.originalA;
    _SW.b = _SW.originalB;
    return;
  }
  if (_NE.a == 50) return;
  Stop();
  _NE.a = 50;
  _NE.b = 50;
  _NW.a = 50;
  _NW.b = 50;
  _SE.a = 50;
  _SE.b = 50;
  _SW.a = 50;
  _SW.b = 50;
}

void Motor::pidNorth(int initAngle, int speed) {
  float input = compass -> checkAngle();
  float error = initAngle + input;
  float output = pid.computePID(input, initAngle, error, &stability);
  if (output == 9999) return;
  fNE(speed + output);
  fSE(speed + output);
  fNW(speed - output);
  fSW(speed - output);
}

void Motor::pidSouth(int initAngle, int speed) {
  speed *= -1;
  float input = compass -> checkAngle();
  float error = initAngle + input;
  float output = pid.computePID(input, initAngle, error, &stability);
  if (output == 9999) return;
  fNW(speed - output);
  fSW(speed - output);
  fNE(speed + output);
  fSE(speed + output);
}

void Motor::pidEast(int initAngle, int speed) {
  float input = compass -> checkAngle();
  float error = initAngle + input;
  float output = pid.computePID(input, initAngle, error, &stability);
  if (output == 9999) return;
  fNW(speed - output);
  fNE(-speed + output);
  fSW(-speed - output);
  fSE(speed + output);
}

void Motor::pidWest(int initAngle, int speed) {
  float input = compass -> checkAngle();
  float error = initAngle + input;
  float output = pid.computePID(input, initAngle, error, &stability);
  if (output == 9999) return;
  fNW(-speed - output);
  fNE(speed + output);
  fSW(speed - output);
  fSE(-speed + output);
}


void Motor::moveToAngle(int initAngle, int angle, int speed) {
  int NW_speed = speed * cos((PI / 180) * (angle + 315));
  int SW_speed = speed * cos((PI / 180) * (angle + 225));
  int SE_speed = speed * cos((PI / 180) * (angle + 135));
  int NE_speed = speed * cos((PI / 180) * (angle + 45));

  int numbers[] = { abs(NW_speed), abs(SW_speed), abs(SE_speed), abs(NE_speed) };
  int _largestNumber = numbers[0];
  for (int i = 1; i < 4; i++)
    if (numbers[i] > _largestNumber) _largestNumber = numbers[i];
  float ratio = float(speed) / float(_largestNumber);
  NW_speed *= ratio;
  SW_speed *= -ratio;
  SE_speed *= -ratio;
  NE_speed *= ratio;
  fNW(NW_speed);
  fSW(SW_speed);
  fSE(SE_speed);
  fNE(NE_speed);
}

void Motor::NorthWest(int speed) {
  fNE(0, speed);
  fSW(0, speed);
  fNW(0, 0);
  fSE(0, 0);
}

void Motor::NorthEast(int speed) {
  fNW(0, speed);
  fSE(0, speed);
  fNE(0, 0);
  fSW(0, 0);
}

void Motor::SouthEast(int speed) {
  fNE(1, speed);
  fSW(1, speed);
  fNW(0, 0);
  fSE(0, 0);
}

void Motor::SouthWest(int speed) {
  fNW(1, speed);
  fSE(1, speed);
  fNE(0, 0);
  fSW(0, 0);
}

void Motor::North(int speed) {
  fNW(0, speed);
  fNE(0, speed);
  fSW(0, speed);
  fSE(0, speed);
}

void Motor::South(int speed) {
  fNW(1, speed);
  fNE(1, speed);
  fSW(1, speed);
  fSE(1, speed);
}

void Motor::East(int speed) {
  fNW(0, speed);
  fNE(1, speed);
  fSW(1, speed);
  fSE(0, speed);
}

void Motor::West(int speed) {
  fNW(1, speed);
  fNE(0, speed);
  fSW(0, speed);
  fSE(1, speed);
}

void Motor::TurnLeft(int speed) {
  fNW(1, speed);
  fNE(0, speed);
  fSW(1, speed);
  fSE(0, speed);
  rotation = 0;
};

void Motor::TurnRight(int speed) {
  fNW(0, speed);
  fNE(1, speed);
  fSW(0, speed);
  fSE(1, speed);
  rotation = 1;
};
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

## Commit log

2023-02-26 Added Eagle boards and structure folders
    [ControlBoardV2_PRO.brd, ControlBoardV2_PRO.sch]
2023-03-02 First commit (Arduino files)
2023-03-04 Added Eagle PCBs
    V1 and V2 of main board, tutorial board.
    [ArduinoLED.brd, ArduinoLED.sch, ArduinoUNOinBoard.brd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]
2023-04-14 Camera calibration scripts
2023-04-14 Librería de motores actualizada para monster drivers
2023-04-17 Added program to convert LSM readings to navx-like
    [ArduinoLED.brd, ArduinoLED.sch, ArduinoUNOinBoard.brd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]
2023-04-17 Uploaded Boards
    [ControlBoardV2_PRO.brd, ControlBoardV2_PRO.sch, Sensors_Board_V1.brd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]
2023-04-23 Últimos cambios, prototipo de robot atacante estable
2023-05-14 Nuevo sistema de comunicación entre Arduino y OpenMV (beta)
2023-05-18 Motor brushless prueba
2023-05-23 Primera base para 4to modelo
2023-05-27 Nueva librería de OpenMV y rediseño de estrategias
2023-06-04 Emulador de robot (Xbee)
2023-06-24 Prototipos funcionales de ambos robots para mundial rcj 2023
2023-06-24 Error de memoria dinámica de variables locales resuelto
    [Camera.cpp, Compass.cpp, Motor.cpp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]

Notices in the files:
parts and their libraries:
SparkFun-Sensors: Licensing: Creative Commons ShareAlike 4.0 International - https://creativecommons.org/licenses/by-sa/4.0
